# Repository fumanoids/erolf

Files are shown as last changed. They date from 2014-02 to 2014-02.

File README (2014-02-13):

              README FOR THE EROLF HARD- AND SOFTWARE RELEASE
            ===================================================

             2014-02-13 FUmanoids' Erolf Hardware Release v2014

          Copyright (c) 2014 FUmanoids / Freie Universität Berlin
                            All rights reserved

        For full license information, please refer to file LICENCE

Links:
       FUmanoids Homepage                           http://www.fumanoids.de
       FUmanoids on Facebook              http://www.facebook.com/fumanoids
       FUmanoids on Twitter                    http://twitter.com/fumanoids

       RoboCup Homepage                              http://www.robocup.org
       RoboCup Humanoid League Homepage          http://www.tzi.de/humanoid

This is part of the code/hardware release of team FUmanoids, version 2014. 

Our goal by releasing the source code and CAD files of components of our robot
is to provide some insight in humanoid soccer robot development, allowing other
teams to learn from our code and possibly our mistakes, but also to hopefully
encourage them to do the same and release their code as well. Though RoboCup is
a competition, it's also about research and finally to achieve our common goal -
to win against FIFA in 2050 ...

 1. PROJECT STRUCTURE
----------------------

The FUmanoids team has developed several software applications as well as our
own robots. The latter was developed internally and equipped with both
commercially available and self-built electronics.

This release addresses only the custom-built microcontroller board (named Erolf) 
used in the FUmanoid robots.

Neither a compiler, an SDK or CAD software is part of this package. In the
section "Getting Started" you find a list of recommended software to modify or
view the CAD files, to compile the software and to put the binaries onto the
processors.

 1.1 Overview of the package
-----------------------------

The project's root directory is "erolf" (the board's name).

The directories in the root directory are:

 - bin      -- some useful scripts and programs for building the program and
               documentation
 - build    -- All binary files of the program go here. This directory will
               be created during code compilation.
 - doc      -- The documentation directory. Here you can find some 
               documentation of the board. There are png files containing
               the schematics and the layout.
 - src      -- The actual source code.
               Note: The essential parts of the software is pretty well
               documented. Please consider this as a documentation 
               directory as well.
 - hardware -- Here you can find the CAD files for the PCB.

 2. THE EROLF PROJECT
------------------------- 

 2.1 Getting Started
-------------------------

 2.1.1 Software

The software is written in C with two extensions in assembler
(system_mutex_lock() and system_mutex_unlock()).

A compiler for the target hardware is not part of this package but can be picked
based on the user's preferences. We recommend using the arm-none-eabi-toolchain
(including gcc, ld and gdb) which can be found here:

                  https://launchpad.net/gcc-arm-embedded

 2.1.2 Hardware

To view the schematics and layout of this project we recommend using "CadSoft
EAGLE" which can be found at: http://www.cadsoftusa.com/

 2.1.3 Manufacturing

The PCB can be manufactured by most commonly known PCB services. A partlist can
be found in the folder where the schematics reside. But please double check the 
partlist since we cannot guarantee its completeness.

We chose every component on the board to be manually solderable. All you need is
a steady hand.

 2.1.4 Other Prerequisites
 
To flash the target a JTAG/SWD interface is needed.

We recommend using a "JLink" from Segger which supports JTAG and SWD for
flashing and debugging. Segger releases software acting as gdb-server and other
tools for common operating systems  (Linux, Mac, Windows). 

 2.2 Compiling the Software
---------------------------

The build system is based on premake 4. We include a more recent binary version
of premake4 than currently available in e.g. Ubuntu.. If you want the sourcecode
of premake have a look at http://industriousone.com/premake. Premake is licenced
under the terms of the BSD License.

The common IDE used for development in team FUmanoids is Eclipse/CDT which
is available at http://www.eclipse.org. Therefore we have the corresponding
project files added to our repository, to give an easy start. You can build the
code either by using Eclipse or by shell tools. Both ways are easy.
Other IDEs or editors can of course be used.

The build process generates two .elf files. One for each processor.

 2.2.1 Using Eclipse

If you choose to use Eclipse click File->Import and in the opening window
General->"Existing Project into Workspace" and choose the project's root
directory. Then you can compile the debug or release version of the software.

 2.2.2 Using the shell tools

You can simply run

 ./bin/compile.sh arm [release/debug]

to compile the code. This runs premake to generate the make-files and
runs "make" with the appropriate targets afterwards.

 2.3 Flashing the target
------------------------

In order to flash and debug the target software a JTAG/SWD Interface is needed.
Connect your debug interface to the processor you want to debug. For the pinning
information please consider looking in the schematics and the pinout information
of your JTAG/SWD interface.

In case you use a "JLink" from Segger start the JLinkGDBServer with the
parameter "-if swd" to use the Serial Wire Debug interface (similar to JTAG but
uses less wires). The output should tell you that a Cortex-M4 was identified.
If your debug interface cannot connect to the target doublecheck the power
supply and the pinning between your debug interface and the connector on
the PCB.

After your GDB-server is running you can use the flash.sh script (in the bin/
directory) to  flash the target. Use "./bin/flash.sh erolfP[1/2].elf".

In case you want to debug the software you can use the command line:

   run "arm-none-eabi-gdb"

In the following prompt enter:

   target remote localhost:2331
   monitor reset 0
   file erolfP[1/2].elf
   load
   monitor reset 0
   continue

In case you use Eclipse you can set up the "GDB Hardware Debugging" plugin for
this as well.

 4. REFERENCES
--------------

The framework used in this software was developed as part of the FUmanoid
project and is used in its power supply board as well (the project can be found
at http://www.fumanoids.de). The Berlin United Racing Team incorporates a
microcontroller board similar to the erolf which is operated by the framework as
well.

Many aspects of our work is described in the corresponding theses of our
students, which are available online at http://www.fumanoids.de/publications,
though most of them are in German.

This software uses libopencm3 which can be found at libopencm3.org.
Thank you very much for this project!

 5. CONTACT
-----------

We'd love to receive feedback, please feel free to contact us by email
at info@fumanoids.de. For information about our team and ongoing progress,
follow us on https://www.facebook.com/fumanoids, https://twitter.com/fumanoids
and http://www.fumanoids.de.

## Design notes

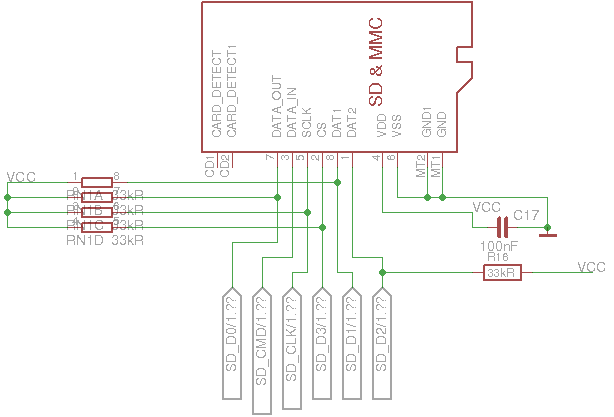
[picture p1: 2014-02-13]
doc/SCHEMATICS_sd_card.png

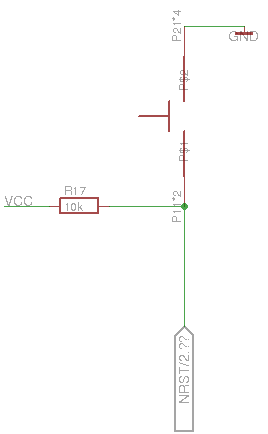
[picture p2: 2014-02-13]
doc/SCHEMATICS_reset_button.png

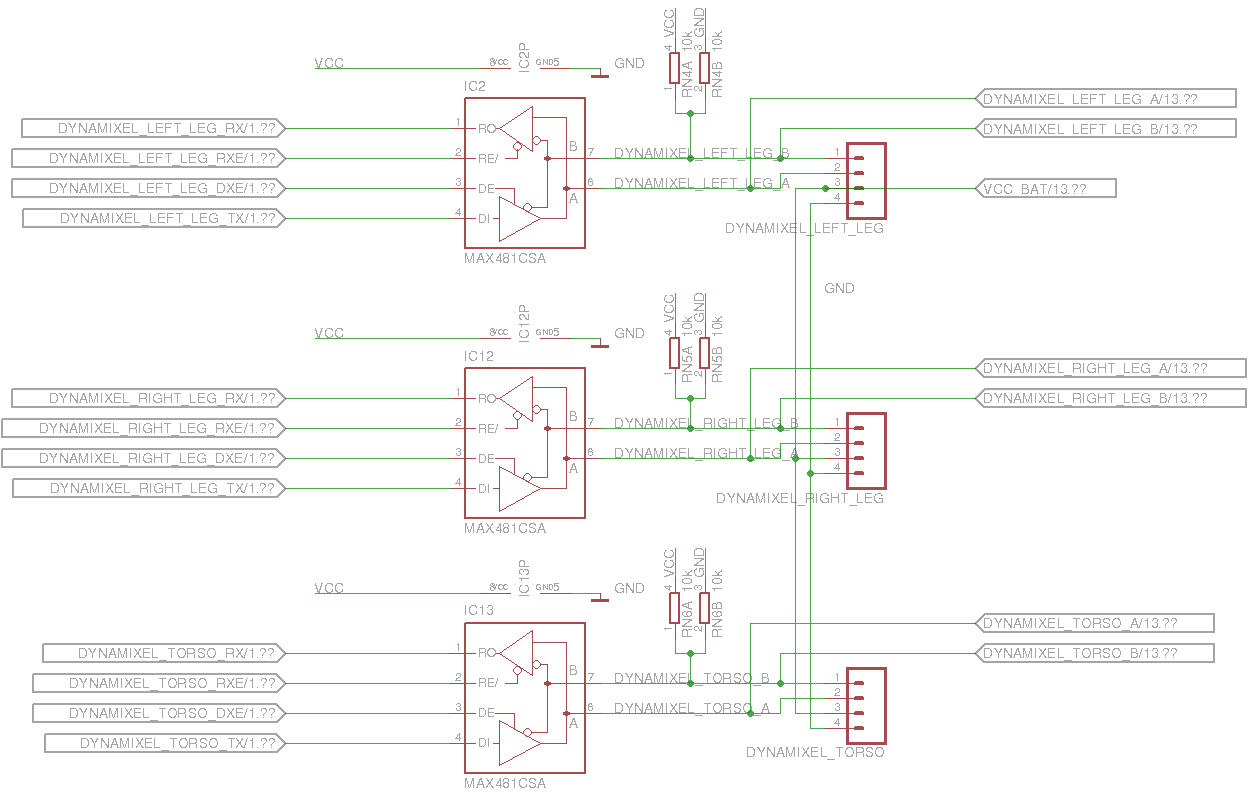
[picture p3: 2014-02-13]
doc/SCHEMATICS_rs485_interfaces.png

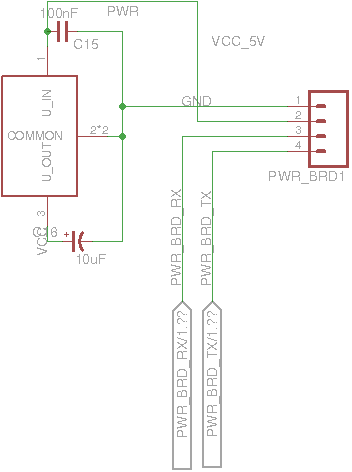
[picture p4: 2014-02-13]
doc/SCHEMATICS_voltage_regulator.png

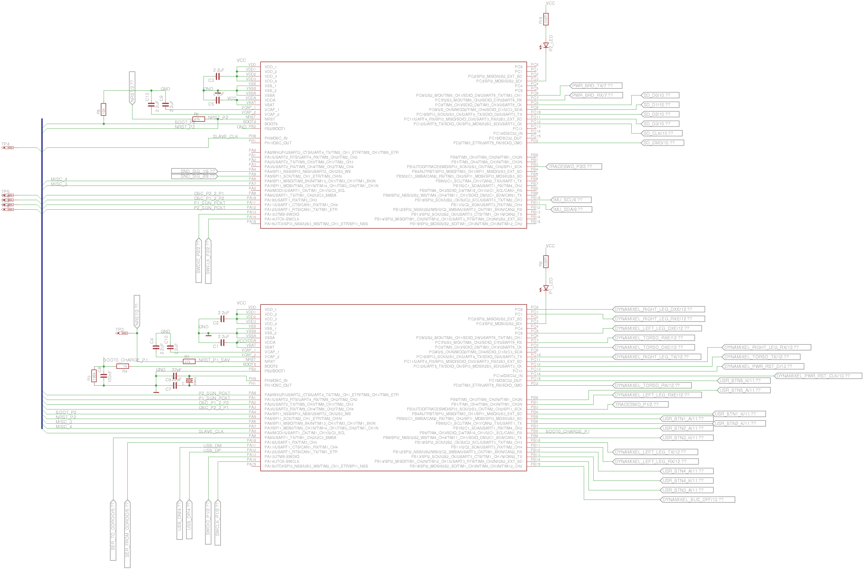
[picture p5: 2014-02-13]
doc/SCHEMATICS_processors.png

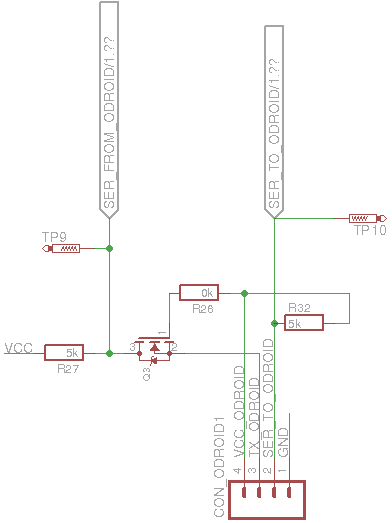
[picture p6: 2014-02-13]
doc/SCHEMATICS_communication_2_main_computer.png

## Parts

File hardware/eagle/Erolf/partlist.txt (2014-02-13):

Partlist

Exported from Erolf2.brd at 15 Aug 2013 12:00:02

EAGLE Version 6.5.0 Copyright (c) 1988-2013 CadSoft

Assembly variant: 

Part                Value              Package         Library                 Position (mm)         Orientation

############################# Kondensatoren

9x
C4                  2.2uF              C0603           rc-master               (10 14)               R90

2x
C6                  22pF               C0603           rc-master               (35 10)               MR180

3x
C8                  100nF              C0603           rc-master               (29 6)                MR0

############################# Stecker

6x
CON_ODROID1                            04P             con-amp-quick           (3 11)                R90

1x
X3                  MINI-USB-32005-301 32005-301       con-cypressindustries   (5.33 23.48)          R0

2x
X1                  53398-06           53398-06        con-molex               (21.96 3.09)          R180

1x
X5                  53398-10           53398-10        con-molex               (42 5)                R0

############################# Diskretes

1x
BLUBB                                  SOT223-4        texas                   (10.82 33.53)         MR270

6x
IC1                 TL331              DBV-R-PDSO-G5   linear                  (47 32)               MR270

3x
IC2                 MAX481CSA          SO08            maxim                   (47 22)               R270

1x
IC11                USB6B1             SO08            st-microelectronics     (10 23)               MR90

2x
P2_LED                                 CHIP-LED0805    adafruit                (29 29)               R0

2x
PROCESSOR_2         STM32-F405RB       LQFP-64         stm32                   (22 35)               R0

3x
Q1                  BSS123             SOT23           transistor-small-signal (40 38)               R0

# D-FF
1x
U$7                                    DCV_R-PDSO-6    texas                   (41.01 32.41)         MR90

# p-MOSFET
1x
U$6                 SI4459ADY          SO-8            vishay                  (46.01 38.23)         MR0

############################# Widerstaende

1x
R3                  100k               R0603           divers                  (25 4)                MR180

7x
R33                 330                R0603           divers                  (38 7)                MR90

6x
R2                  1k                 R0603           divers                  (40 33)               R180

10x
R13                 10k                R0603           divers                  (43 42)               R0

1x
R16                 33kR               R0603           divers                  (38 43)               MR180

1x
RN1                 33kR               EXBS8V          resistor-dil            (35 47)               MR180

4x
RN2                 10k                EXBV4V          resistor-dil            (47 42)               R90

############################# Misc

1x
U$2                 MICROSD            MICROSD         adafruit                (16 32)               MR180

1x
U$3                                    BUTTON          berlinunited            (10 35)               R270

1x
U$4                 MINI-IMU-9V2       PCB             miniIMU-9v2             (32 30)               R0

1x
Y1                  8MHz              CRYSTAL_4.9X1.8 microbuilder            (36 13)               R180

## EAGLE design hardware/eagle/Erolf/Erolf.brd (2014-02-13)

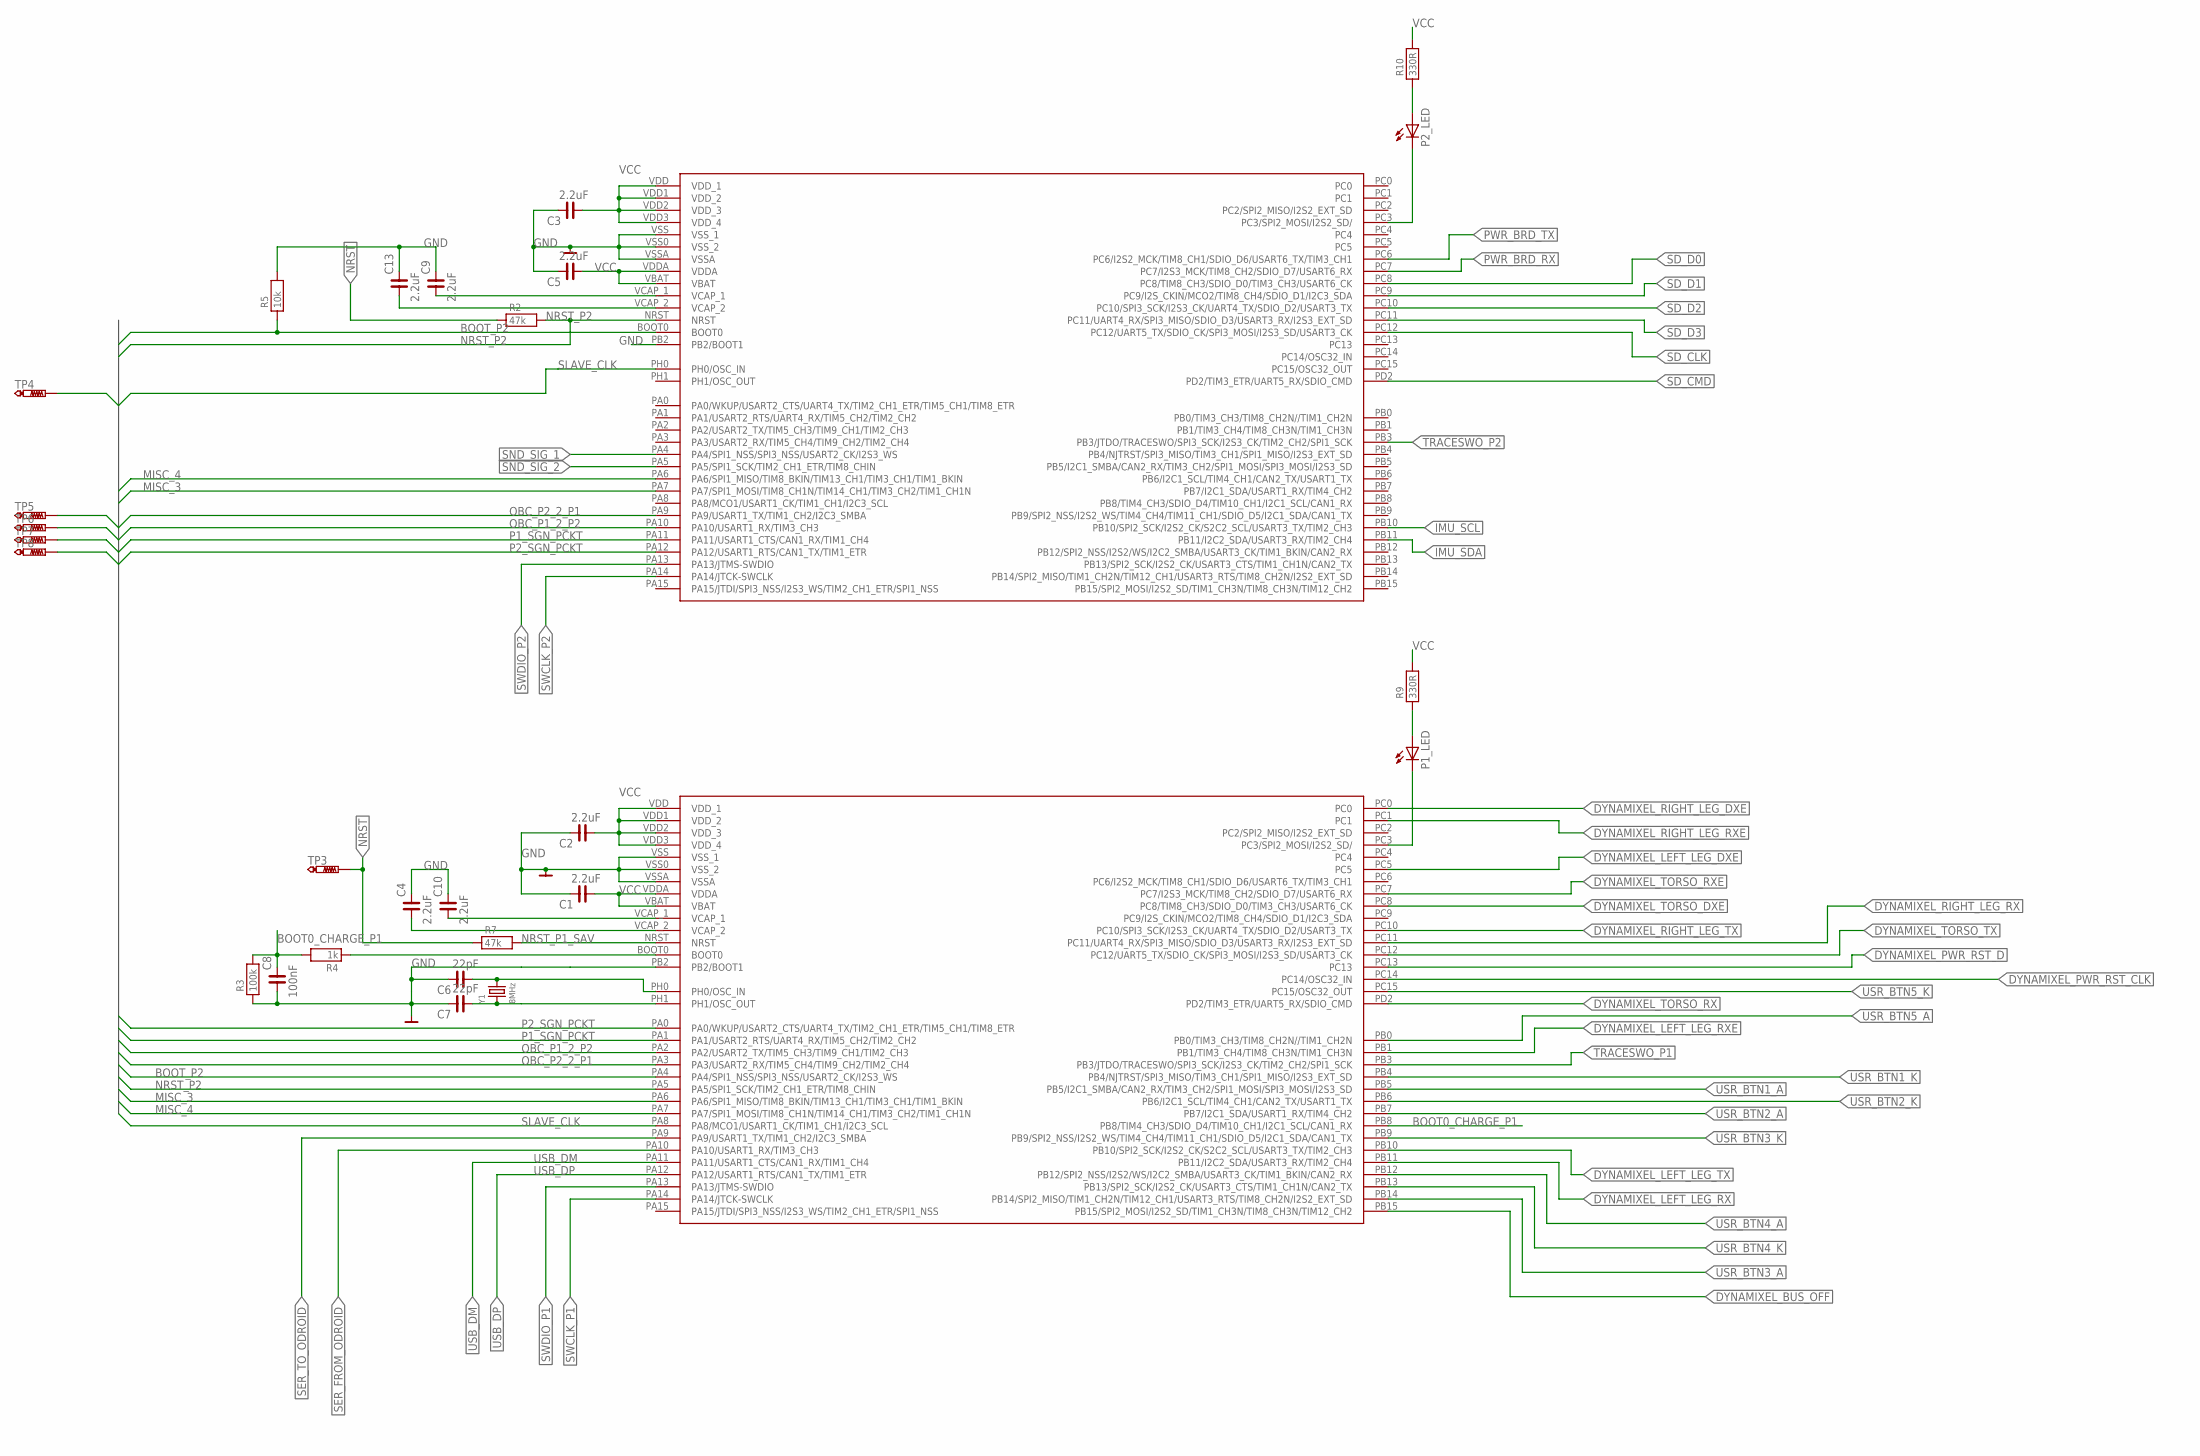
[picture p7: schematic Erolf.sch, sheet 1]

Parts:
C1, C2, C3, C4, C5, C9, C10, C13: 2.2uF; C0603
C6, C7: 22pF; C0603
C8: 100nF; C0603
P1_LED, P2_LED: LEDCHIP-LED0805; CHIP-LED0805
PROCESSOR_1, PROCESSOR_2: STM32-F405RB; LQFP-64
R2, R7: 47k; R0603
R3: 100k; R0603
R4: 1k; R0603
R5: 10k; R0603
R9, R10: 330R; R0603
TP3, TP4, TP5, TP6, TP7, TP8: PTR1TP06R; TP06R
Y1: 8MHz; CRYSTAL_4.9X1.8

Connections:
BOOT0_CHARGE_P1: C8.2, PROCESSOR_1.PB8 (PB8/TIM4_CH3/SDIO_D4/TIM10_CH1/I2C1_SCL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), R3.2, R4.2
BOOT_P2: PROCESSOR_1.PA4 (PA4/SPI1_NSS/SPI3_NSS/USART2_CK/I2S3_WS), PROCESSOR_2.BOOT0, R5.1
DYNAMIXEL_BUS_OFF: PROCESSOR_1.PB15 (PB15/SPI2_MOSI/I2S2_SD/TIM1_CH3N/TIM8_C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); also elsewhere on the board
DYNAMIXEL_LEFT_LEG_DXE: PROCESSOR_1.PC5; also elsewhere on the board
DYNAMIXEL_LEFT_LEG_RX: PROCESSOR_1.PB11 (PB11/I2C2_SDA/USART3_RX/TIM2_CH4); also elsewhere on the board
DYNAMIXEL_LEFT_LEG_RXE: PROCESSOR_1.PB1 (PB1/TIM3_CH4/TIM8_CH3N/TIM1_CH3N); also elsewhere on the board
DYNAMIXEL_LEFT_LEG_TX: PROCESSOR_1.PB10 (PB10/SPI2_SCK/I2S2_CK/S2C2_SCL/USART3_T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); also elsewhere on the board
DYNAMIXEL_PWR_RST_CLK: PROCESSOR_1.PC14 (PC14/OSC32_IN); also elsewhere on the board
DYNAMIXEL_PWR_RST_D: PROCESSOR_1.PC13; also elsewhere on the board
DYNAMIXEL_RIGHT_LEG_DXE: PROCESSOR_1.PC0; also elsewhere on the board
DYNAMIXEL_RIGHT_LEG_RX: PROCESSOR_1.PC11 (PC11/UART4_RX/SPI3_MISO/SDIO_D3/USART3_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); also elsewhere on the board
DYNAMIXEL_RIGHT_LEG_RXE: PROCESSOR_1.PC1; also elsewhere on the board
DYNAMIXEL_RIGHT_LEG_TX: PROCESSOR_1.PC10 (PC10/SPI3_SCK/I2S3_CK/UART4_TX/SDIO_D2/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); also elsewhere on the board
DYNAMIXEL_TORSO_DXE: PROCESSOR_1.PC8 (PC8/TIM8_CH3/SDIO_D0/TIM3_CH3/USART6_CK); also elsewhere on the board
DYNAMIXEL_TORSO_RX: PROCESSOR_1.PD2 (PD2/TIM3_ETR/UART5_RX/SDIO_CMD); also elsewhere on the board
DYNAMIXEL_TORSO_RXE: PROCESSOR_1.PC7 (PC7/I2S3_MCK/TIM8_CH2/SDIO_D7/USART6_RX); also elsewhere on the board
DYNAMIXEL_TORSO_TX: PROCESSOR_1.PC12 (PC12/UART5_TX/SDIO_CK/SPI3_MOSI/I2S3_SD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); also elsewhere on the board
GND: C1.2, C2.2, C3.2, C4.2, C5.2, C6.2, C7.2, C8.1, C9.2, C10.2, C13.2, PROCESSOR_1.PB2 (PB2/BOOT1), PROCESSOR_1.VSS (VSS_1), PROCESSOR_1.VSS0 (VSS_2), PROCESSOR_1.VSSA, PROCESSOR_2.PB2 (PB2/BOOT1), PROCESSOR_2.VSS (VSS_1), PROCESSOR_2.VSS0 (VSS_2), PROCESSOR_2.VSSA, R3.1, R5.2; also elsewhere on the board
IMU_SCL: PROCESSOR_2.PB10 (PB10/SPI2_SCK/I2S2_CK/S2C2_SCL/USART3_T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); also elsewhere on the board
IMU_SDA: PROCESSOR_2.PB11 (PB11/I2C2_SDA/USART3_RX/TIM2_CH4); also elsewhere on the board
MISC_3: PROCESSOR_1.PA6 (PA6/SPI1_MISO/TIM8_BKIN/TIM13_CH1/TIM3_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), PROCESSOR_2.PA7 (PA7/SPI1_MOSI/TIM8_CH1N/TIM14_CH1/TIM3_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)
MISC_4: PROCESSOR_1.PA7 (PA7/SPI1_MOSI/TIM8_CH1N/TIM14_CH1/TIM3_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), PROCESSOR_2.PA6 (PA6/SPI1_MISO/TIM8_BKIN/TIM13_CH1/TIM3_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)
unnamed: C10.1, PROCESSOR_1.VCAP_1
unnamed: P1_LED.A, R9.1
unnamed: P2_LED.A, R10.1
unnamed: P1_LED.C, PROCESSOR_1.PC3 (PC3/SPI2_MOSI/I2S2_SD/)
unnamed: C13.1, PROCESSOR_2.VCAP_2
unnamed: C9.1, PROCESSOR_2.VCAP_1
unnamed: PROCESSOR_1.BOOT0, R4.1
unnamed: P2_LED.C, PROCESSOR_2.PC3 (PC3/SPI2_MOSI/I2S2_SD/)
unnamed: C4.1, PROCESSOR_1.VCAP_2
NRST: R2.1, R7.1, TP3.TP; also elsewhere on the board
NRST_P1_SAV: PROCESSOR_1.NRST, R7.2
NRST_P2: PROCESSOR_1.PA5 (PA5/SPI1_SCK/TIM2_CH1_ETR/TIM8_CHIN), PROCESSOR_2.NRST, R2.2
OBC_P1_2_P2: PROCESSOR_1.PA2 (PA2/USART2_TX/TIM5_CH3/TIM9_CH1/TIM2_CH3), PROCESSOR_2.PA10 (PA10/USART1_RX/TIM3_CH3), TP6.TP
OBC_P2_2_P1: PROCESSOR_1.PA3 (PA3/USART2_RX/TIM5_CH4/TIM9_CH2/TIM2_CH4), PROCESSOR_2.PA9 (PA9/USART1_TX/TIM1_CH2/I2C3_SMBA), TP5.TP
OSC_IN: C6.1, PROCESSOR_1.PH0 (PH0/OSC_IN), Y1.2
OSC_OUT: C7.1, PROCESSOR_1.PH1 (PH1/OSC_OUT), Y1.1
P1_SGN_PCKT: PROCESSOR_1.PA1 (PA1/USART2_RTS/UART4_RX/TIM5_CH2/TIM2_C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), PROCESSOR_2.PA11 (PA11/USART1_CTS/CAN1_RX/TIM1_CH4), TP7.TP
P2_SGN_PCKT: PROCESSOR_1.PA0 (PA0/WKUP/USART2_CTS/UART4_TX/TIM2_CH1_E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), PROCESSOR_2.PA12 (PA12/USART1_RTS/CAN1_TX/TIM1_ETR), TP8.TP
PWR_BRD_RX: PROCESSOR_2.PC7 (PC7/I2S3_MCK/TIM8_CH2/SDIO_D7/USART6_RX); also elsewhere on the board
PWR_BRD_TX: PROCESSOR_2.PC6 (PC6/I2S2_MCK/TIM8_CH1/SDIO_D6/USART6_TX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); also elsewhere on the board
SD_CLK: PROCESSOR_2.PC12 (PC12/UART5_TX/SDIO_CK/SPI3_MOSI/I2S3_SD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); also elsewhere on the board
SD_CMD: PROCESSOR_2.PD2 (PD2/TIM3_ETR/UART5_RX/SDIO_CMD); also elsewhere on the board
SD_D0: PROCESSOR_2.PC8 (PC8/TIM8_CH3/SDIO_D0/TIM3_CH3/USART6_CK); also elsewhere on the board
SD_D1: PROCESSOR_2.PC9 (PC9/I2S_CKIN/MCO2/TIM8_CH4/SDIO_D1/I2C3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); also elsewhere on the board
SD_D2: PROCESSOR_2.PC10 (PC10/SPI3_SCK/I2S3_CK/UART4_TX/SDIO_D2/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); also elsewhere on the board
SD_D3: PROCESSOR_2.PC11 (PC11/UART4_RX/SPI3_MISO/SDIO_D3/USART3_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); also elsewhere on the board
SER_FROM_ODROID: PROCESSOR_1.PA10 (PA10/USART1_RX/TIM3_CH3); also elsewhere on the board
SER_TO_ODROID: PROCESSOR_1.PA9 (PA9/USART1_TX/TIM1_CH2/I2C3_SMBA); also elsewhere on the board
SLAVE_CLK: PROCESSOR_1.PA8 (PA8/MCO1/USART1_CK/TIM1_CH1/I2C3_SCL), PROCESSOR_2.PH0 (PH0/OSC_IN), TP4.TP
SND_SIG_1: PROCESSOR_2.PA4 (PA4/SPI1_NSS/SPI3_NSS/USART2_CK/I2S3_WS); also elsewhere on the board
SND_SIG_2: PROCESSOR_2.PA5 (PA5/SPI1_SCK/TIM2_CH1_ETR/TIM8_CHIN); also elsewhere on the board
SWCLK_P1: PROCESSOR_1.PA14 (PA14/JTCK-SWCLK); also elsewhere on the board
SWCLK_P2: PROCESSOR_2.PA14 (PA14/JTCK-SWCLK); also elsewhere on the board
SWDIO_P1: PROCESSOR_1.PA13 (PA13/JTMS-SWDIO); also elsewhere on the board
SWDIO_P2: PROCESSOR_2.PA13 (PA13/JTMS-SWDIO); also elsewhere on the board
TRACESWO_P1: PROCESSOR_1.PB3 (PB3/JTDO/TRACESWO/SPI3_SCK/I2S3_CK/TIM2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); also elsewhere on the board
TRACESWO_P2: PROCESSOR_2.PB3 (PB3/JTDO/TRACESWO/SPI3_SCK/I2S3_CK/TIM2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); also elsewhere on the board
USB_DM: PROCESSOR_1.PA11 (PA11/USART1_CTS/CAN1_RX/TIM1_CH4); also elsewhere on the board
USB_DP: PROCESSOR_1.PA12 (PA12/USART1_RTS/CAN1_TX/TIM1_ETR); also elsewhere on the board
USR_BTN1_A: PROCESSOR_1.PB5 (PB5/I2C1_SMBA/CAN2_RX/TIM3_CH2/SPI1_MOS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); also elsewhere on the board
USR_BTN1_K: PROCESSOR_1.PB4 (PB4/NJTRST/SPI3_MISO/TIM3_CH1/SPI1_MISO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); also elsewhere on the board
USR_BTN2_A: PROCESSOR_1.PB7 (PB7/I2C1_SDA/USART1_RX/TIM4_CH2); also elsewhere on the board
USR_BTN2_K: PROCESSOR_1.PB6 (PB6/I2C1_SCL/TIM4_CH1/CAN2_TX/USART1_TX); also elsewhere on the board
USR_BTN3_A: PROCESSOR_1.PB14 (PB14/SPI2_MISO/TIM1_CH2N/TIM12_CH1/USAR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); also elsewhere on the board
USR_BTN3_K: PROCESSOR_1.PB9 (PB9/SPI2_NSS/I2S2_WS/TIM4_CH4/TIM11_CH1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); also elsewhere on the board
USR_BTN4_A: PROCESSOR_1.PB12 (PB12/SPI2_NSS/I2S2/WS/I2C2_SMBA/USART3_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); also elsewhere on the board
USR_BTN4_K: PROCESSOR_1.PB13 (PB13/SPI2_SCK/I2S2_CK/USART3_CTS/TIM1_C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); also elsewhere on the board
USR_BTN5_A: PROCESSOR_1.PB0 (PB0/TIM3_CH3/TIM8_CH2N//TIM1_CH2N); also elsewhere on the board
USR_BTN5_K: PROCESSOR_1.PC15 (PC15/OSC32_OUT); also elsewhere on the board
VCC: C1.1, C2.1, C3.1, C5.1, PROCESSOR_1.VBAT, PROCESSOR_1.VDD (VDD_1), PROCESSOR_1.VDD1 (VDD_2), PROCESSOR_1.VDD2 (VDD_3), PROCESSOR_1.VDD3 (VDD_4), PROCESSOR_1.VDDA, PROCESSOR_2.VBAT, PROCESSOR_2.VDD (VDD_1), PROCESSOR_2.VDD1 (VDD_2), PROCESSOR_2.VDD2 (VDD_3), PROCESSOR_2.VDD3 (VDD_4), PROCESSOR_2.VDDA, R9.2, R10.2; also elsewhere on the board

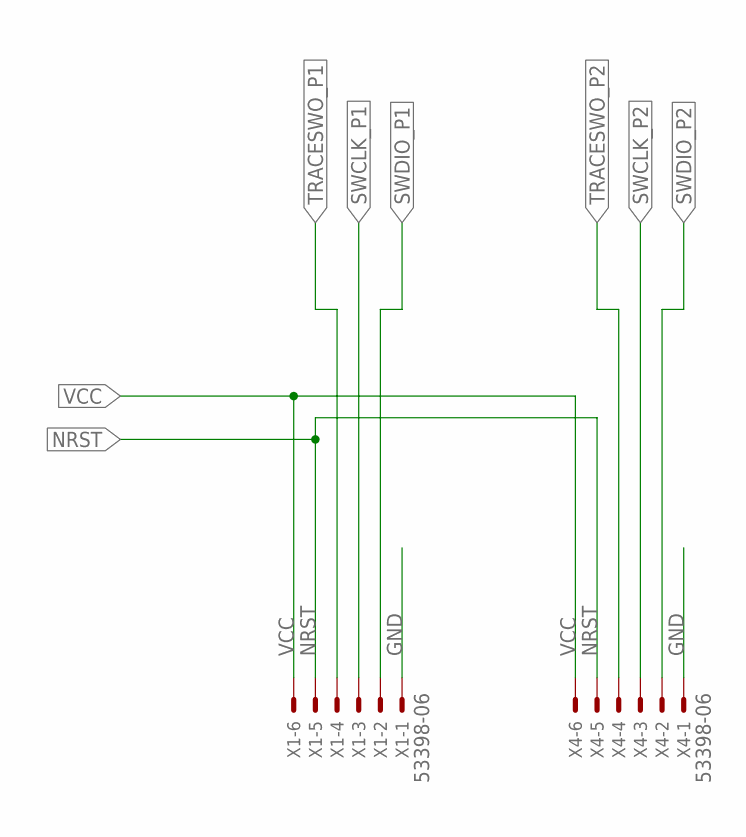
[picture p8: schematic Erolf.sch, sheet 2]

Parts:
X1, X4: 53398-06

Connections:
GND: X1.1, X4.1; also elsewhere on the board
NRST: X1.5, X4.5; also elsewhere on the board
SWCLK_P1: X1.3; also elsewhere on the board
SWCLK_P2: X4.3; also elsewhere on the board
SWDIO_P1: X1.2; also elsewhere on the board
SWDIO_P2: X4.2; also elsewhere on the board
TRACESWO_P1: X1.4; also elsewhere on the board
TRACESWO_P2: X4.4; also elsewhere on the board
VCC: X1.6, X4.6; also elsewhere on the board

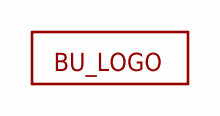
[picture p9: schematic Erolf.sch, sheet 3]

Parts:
U$8: LOGO

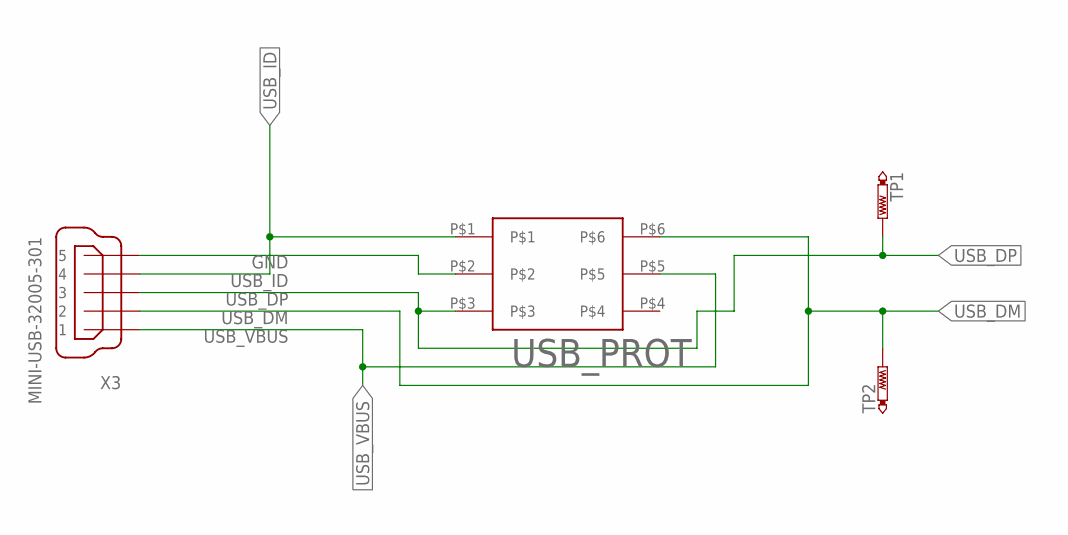
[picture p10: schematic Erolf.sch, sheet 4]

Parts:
TP1, TP2: PTR1TP06R; TP06R
USB_PROT: VBUS054B; LLP75-6L; DIGIKEY 751-1453-1-ND
X3: MINI-USB-32005-301; 32005-301

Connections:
GND: USB_PROT.P$2, X3.5; also elsewhere on the board
USB_DM: TP2.TP, USB_PROT.P$6, X3.2; also elsewhere on the board
USB_DP: TP1.TP, USB_PROT.P$3, X3.3; also elsewhere on the board
USB_ID: USB_PROT.P$1, X3.4
USB_VBUS: USB_PROT.P$5, X3.1

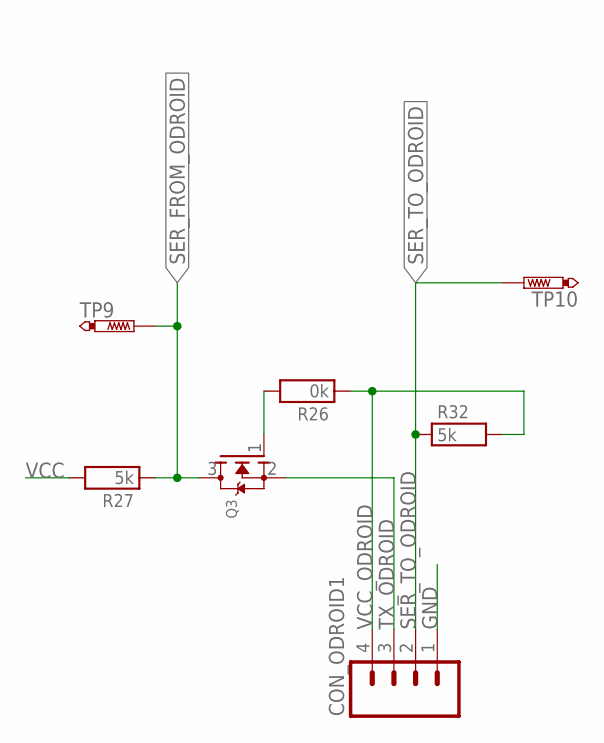
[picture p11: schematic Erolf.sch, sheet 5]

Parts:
CON_ODROID1: M04; 04P
Q3: MOSFET-NREFLOW; SOT23
R26: 0k; R0603
R27, R32: 5k; R0603
TP9, TP10: PTR1TP06R; TP06R

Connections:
GND: CON_ODROID1.1; also elsewhere on the board
unnamed: Q3.1 (G), R26.2
SER_FROM_ODROID: Q3.3 (D), R27.1, TP9.TP; also elsewhere on the board
SER_TO_ODROID: CON_ODROID1.2, R32.1, TP10.TP; also elsewhere on the board
TX_ODROID: CON_ODROID1.3, Q3.2 (S)
VCC: R27.2; also elsewhere on the board
VCC_ODROID: CON_ODROID1.4, R26.1, R32.2

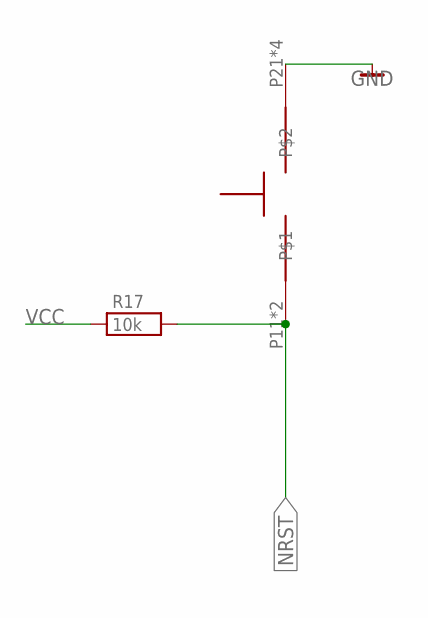
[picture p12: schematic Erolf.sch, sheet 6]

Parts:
R17: 10k; R0603
U$3: BUTTON

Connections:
GND: U$3.P21, U$3.P22, U$3.P23, U$3.P24; also elsewhere on the board
NRST: R17.2, U$3.P11, U$3.P12; also elsewhere on the board
VCC: R17.1; also elsewhere on the board

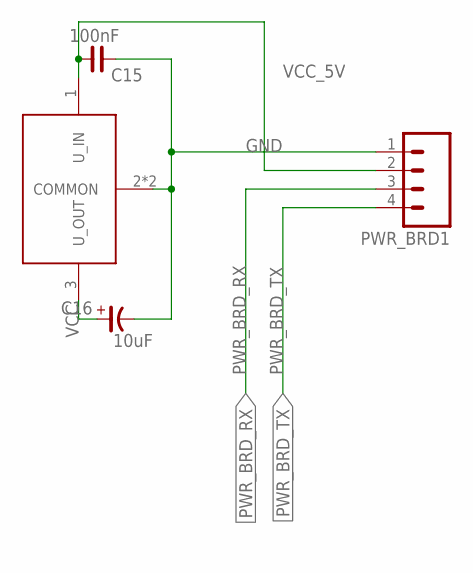
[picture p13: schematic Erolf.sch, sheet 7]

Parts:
BLUBB: UA78M00; SOT223-4
C15: 100nF; C0603
C16: 10uF; CE-025X060
PWR_BRD1: M04; 04P

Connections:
GND: BLUBB.2 (COMMON), BLUBB.4 (COMMON), C15.2, C16.-, PWR_BRD1.1; also elsewhere on the board
PWR_BRD_RX: PWR_BRD1.3; also elsewhere on the board
PWR_BRD_TX: PWR_BRD1.4; also elsewhere on the board
VCC: BLUBB.3 (U_OUT), C16.+; also elsewhere on the board
VCC_5V: BLUBB.1 (U_IN), C15.1, PWR_BRD1.2; also elsewhere on the board

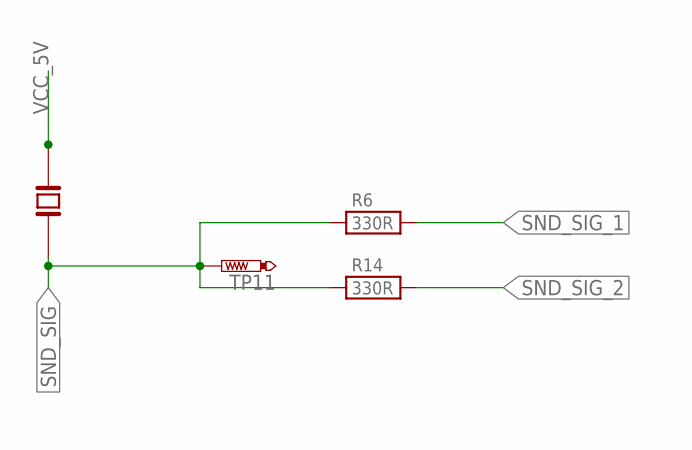
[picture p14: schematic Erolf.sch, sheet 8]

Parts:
R6, R14: 330R; R0603
TP11: PTR1TP06R; TP06R
U$1: PS1240P02CT3

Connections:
SND_SIG: R6.1, R14.1, TP11.TP, U$1.P$2
SND_SIG_1: R6.2; also elsewhere on the board
SND_SIG_2: R14.2; also elsewhere on the board
VCC_5V: U$1.P$1; also elsewhere on the board

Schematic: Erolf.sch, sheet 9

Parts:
U$4: MINI-IMU-9V2; PCB

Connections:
GND: U$4.GND; also elsewhere on the board
IMU_SCL: U$4.SCL; also elsewhere on the board
IMU_SDA: U$4.SDA; also elsewhere on the board
VCC: U$4.VDD, U$4.VIN; also elsewhere on the board

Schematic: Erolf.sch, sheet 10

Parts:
C17: 100nF; C0603
R16: 33kR; R0603
RN1: 33kR; EXBS8V
U$2: MICROSD

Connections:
GND: C17.2, U$2.6 (VSS), U$2.MT1 (GND), U$2.MT2 (GND1); also elsewhere on the board
SD_CLK: RN1.6 (2), U$2.5 (SCLK); also elsewhere on the board
SD_CMD: U$2.3 (DATA_IN); also elsewhere on the board
SD_D0: RN1.7 (2), U$2.7 (DATA_OUT); also elsewhere on the board
SD_D1: RN1.8 (2), U$2.8 (DAT1); also elsewhere on the board
SD_D2: R16.1, U$2.1 (DAT2); also elsewhere on the board
SD_D3: RN1.5 (2), U$2.2 (CS); also elsewhere on the board
VCC: C17.1, R16.2, RN1.1, RN1.2 (1), RN1.3 (1), RN1.4 (1), U$2.4 (VDD); also elsewhere on the board

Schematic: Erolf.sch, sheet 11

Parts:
R1, R8, R11, R12, R33: 330R; R0603
R34, R35, R36, R37, R38: 10kR; R0603
X2: 53261-10

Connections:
USR_BTN1_A: R38.2, X2.9; also elsewhere on the board
USR_BTN1_K: R33.1, X2.10; also elsewhere on the board
USR_BTN2_A: R37.2, X2.7; also elsewhere on the board
USR_BTN2_K: R12.1, X2.8; also elsewhere on the board
USR_BTN3_A: R36.2, X2.5; also elsewhere on the board
USR_BTN3_K: R11.1, X2.6; also elsewhere on the board
USR_BTN4_A: R35.2, X2.3; also elsewhere on the board
USR_BTN4_K: R8.1, X2.4; also elsewhere on the board
USR_BTN5_A: R34.2, X2.1; also elsewhere on the board
USR_BTN5_K: R1.1, X2.2; also elsewhere on the board
VCC: R1.2, R8.2, R11.2, R12.2, R33.2, R34.1, R35.1, R36.1, R37.1, R38.1; also elsewhere on the board

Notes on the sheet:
when using buttons with embedded LED connect the LED's anode with one pin of the button and the LED's cathode with the other pin of the button. The LED's anode shall be connected to USR_BTNx_A and the cathode to USR_BTNx_K

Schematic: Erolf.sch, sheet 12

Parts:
DYNAMIXEL_LEFT_LEG: M04; 04P
DYNAMIXEL_RIGHT_LEG: M04; 04P
DYNAMIXEL_TORSO: M04; 04P
IC2, IC12, IC13: MAX481CSA; SO08
RN4, RN5, RN6: 10k; EXBV4V

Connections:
DYNAMIXEL_LEFT_LEG_A: DYNAMIXEL_LEFT_LEG.2, IC2.6 (A); also elsewhere on the board
DYNAMIXEL_LEFT_LEG_B: DYNAMIXEL_LEFT_LEG.1, IC2.7 (B), RN4.1, RN4.2 (1); also elsewhere on the board
DYNAMIXEL_LEFT_LEG_DXE: IC2.3 (DE); also elsewhere on the board
DYNAMIXEL_LEFT_LEG_RX: IC2.1 (RO); also elsewhere on the board
DYNAMIXEL_LEFT_LEG_RXE: IC2.2 (RE/); also elsewhere on the board
DYNAMIXEL_LEFT_LEG_TX: IC2.4 (DI); also elsewhere on the board
DYNAMIXEL_RIGHT_LEG_A: DYNAMIXEL_RIGHT_LEG.2, IC12.6 (A); also elsewhere on the board
DYNAMIXEL_RIGHT_LEG_B: DYNAMIXEL_RIGHT_LEG.1, IC12.7 (B), RN5.1, RN5.2 (1); also elsewhere on the board
DYNAMIXEL_RIGHT_LEG_DXE: IC12.3 (DE); also elsewhere on the board
DYNAMIXEL_RIGHT_LEG_RX: IC12.1 (RO); also elsewhere on the board
DYNAMIXEL_RIGHT_LEG_RXE: IC12.2 (RE/); also elsewhere on the board
DYNAMIXEL_RIGHT_LEG_TX: IC12.4 (DI); also elsewhere on the board
DYNAMIXEL_TORSO_A: DYNAMIXEL_TORSO.2, IC13.6 (A); also elsewhere on the board
DYNAMIXEL_TORSO_B: DYNAMIXEL_TORSO.1, IC13.7 (B), RN6.1, RN6.2 (1); also elsewhere on the board
DYNAMIXEL_TORSO_DXE: IC13.3 (DE); also elsewhere on the board
DYNAMIXEL_TORSO_RX: IC13.1 (RO); also elsewhere on the board
DYNAMIXEL_TORSO_RXE: IC13.2 (RE/); also elsewhere on the board
DYNAMIXEL_TORSO_TX: IC13.4 (DI); also elsewhere on the board
GND: DYNAMIXEL_LEFT_LEG.4, DYNAMIXEL_RIGHT_LEG.4, DYNAMIXEL_TORSO.4, IC2.5 (GND), IC12.5 (GND), IC13.5 (GND), RN4.3 (2), RN5.3 (2), RN6.3 (2); also elsewhere on the board
VCC: IC2.8 (VCC), IC12.8 (VCC), IC13.8 (VCC), RN4.4 (2), RN5.4 (2), RN6.4 (2); also elsewhere on the board
VCC_BAT: DYNAMIXEL_LEFT_LEG.3, DYNAMIXEL_RIGHT_LEG.3, DYNAMIXEL_TORSO.3; also elsewhere on the board

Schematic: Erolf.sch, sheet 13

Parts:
C11: 100nF; C0603
D1: ZENER-DIODESOD80C; SOD80C
D2: DIODE-MICROMELF-R; MICROMELF-R
DYNAMIXEL_PWR: M04; 04P
IC1, IC3, IC4, IC5, IC6, IC7: TL331; DBV-R-PDSO-G5
Q1: BSS123; SOT23
R13, R18, R23: 10kR; R0603
R15: 1kR; R0603
TP20, TP21, TP22: PTR1TP06R; TP06R
U$6: SI4459ADY; SO-8
U$7: SN74LVC1G175; DCV_R-PDSO-6

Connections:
DYNAMIXEL_BUS_OFF: Q1.1 (G), R15.2; also elsewhere on the board
DYNAMIXEL_BUS_OFF_AUTO_TRIG: IC1.4 (OUT), IC3.4 (OUT), IC4.4 (OUT), IC5.4 (OUT), IC6.4 (OUT), IC7.4 (OUT), R23.2, TP20.TP, U$7.P$6 (NCLR)
DYNAMIXEL_LEFT_LEG_A: IC5.1 (-IN); also elsewhere on the board
DYNAMIXEL_LEFT_LEG_B: IC6.1 (-IN); also elsewhere on the board
DYNAMIXEL_PWR_RST_CLK: U$7.P$1 (CLK); also elsewhere on the board
DYNAMIXEL_PWR_RST_D: U$7.P$3 (D); also elsewhere on the board
DYNAMIXEL_RIGHT_LEG_A: IC4.1 (-IN); also elsewhere on the board
DYNAMIXEL_RIGHT_LEG_B: IC3.1 (-IN); also elsewhere on the board
DYNAMIXEL_TORSO_A: DYNAMIXEL_PWR.2, IC7.1 (-IN); also elsewhere on the board
DYNAMIXEL_TORSO_B: DYNAMIXEL_PWR.1, IC1.1 (-IN); also elsewhere on the board
GND: C11.2, D1.A, DYNAMIXEL_PWR.4, IC1.2 (GND), IC3.2 (GND), IC4.2 (GND), IC5.2 (GND), IC6.2 (GND), IC7.2 (GND), Q1.2 (S), U$7.P$2 (GND); also elsewhere on the board
unnamed: R15.1, U$7.P$4 (Q)
unnamed: Q1.3 (D), R13.1, U$6.P4 (G)
unnamed: D2.C, R18.1
VCC: R23.1, U$7.P$5 (VCC); also elsewhere on the board
VCC_BAT: TP22.TP, U$6.P5 (D), U$6.P6 (D), U$6.P7 (D), U$6.P8 (D); also elsewhere on the board
VCC_BAT_PRE: D2.A, DYNAMIXEL_PWR.3, IC1.5 (V+), IC3.5 (V+), IC4.5 (V+), IC5.5 (V+), IC6.5 (V+), IC7.5 (V+), R13.2, U$6.P1 (S), U$6.P2 (S), U$6.P3 (S)
V_SAFETY_REF: C11.1, D1.C, IC1.3 (+IN), IC3.3 (+IN), IC4.3 (+IN), IC5.3 (+IN), IC6.3 (+IN), IC7.3 (+IN), R18.2, TP21.TP

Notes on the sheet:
the recommended value of this Z-Diode is about the maximum allowed voltage of the RS485 transceivers (usually 12V) minus some margin (2V suffice) 10 Volts is usually a good measure

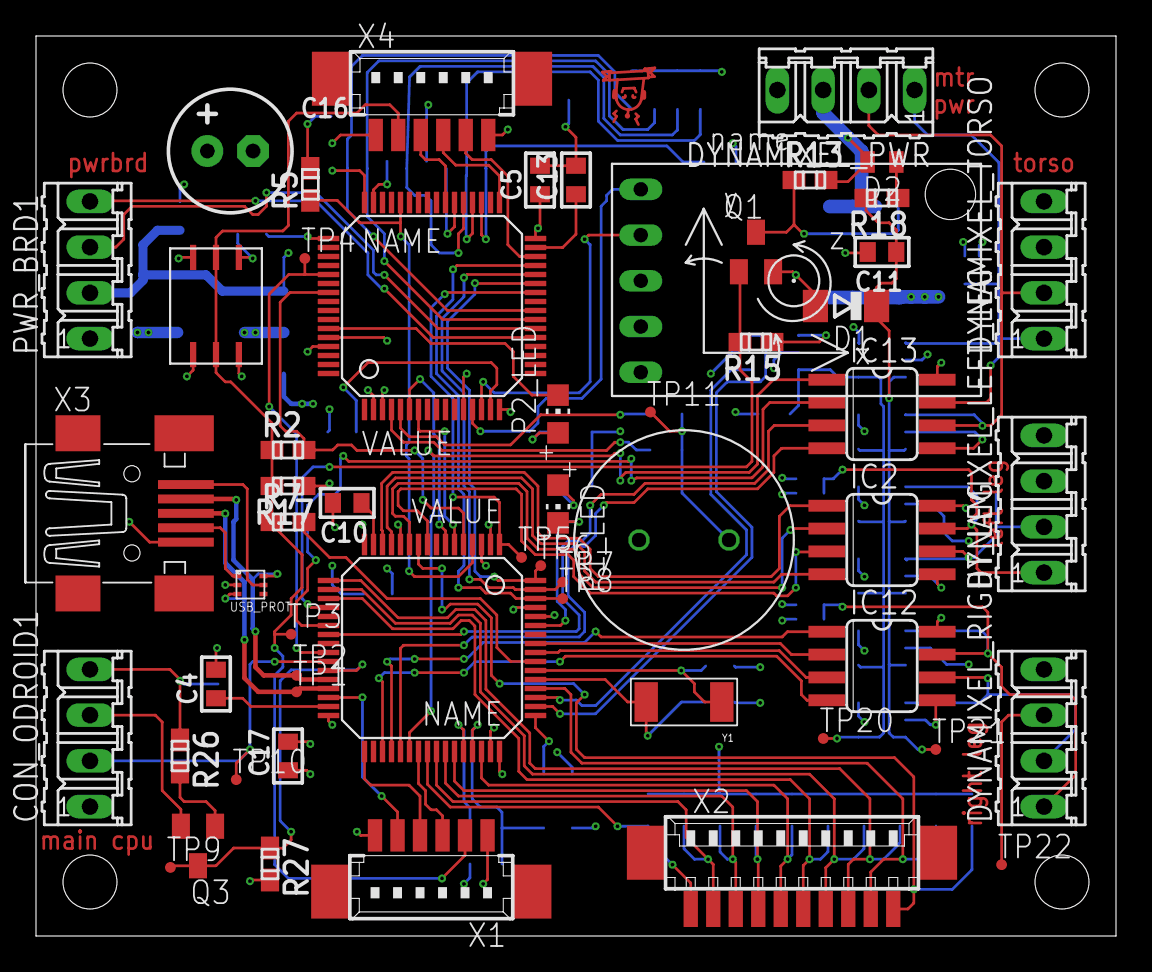
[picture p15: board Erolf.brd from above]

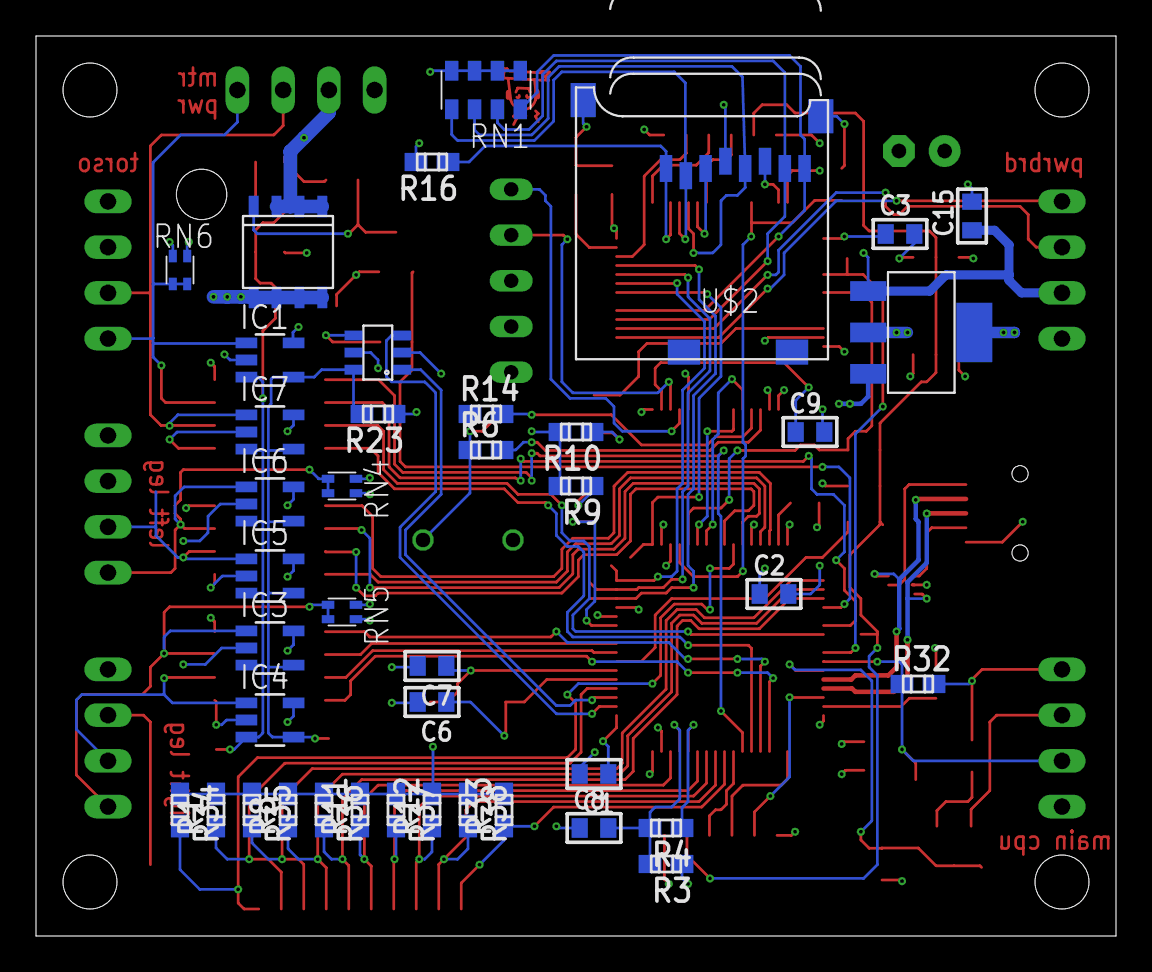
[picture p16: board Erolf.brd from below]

Board: 4 copper layers, 60.0 x 50.0 mm, 98 parts (41 on the bottom side), 92 nets.

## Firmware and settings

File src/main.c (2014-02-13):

/*
 * main.c
 *
 *  Created on: Oct 17, 2012
 *      Author: lutz
 */

#include <flawless/init/systemInitializer.h>

#include <flawless/core/msg_msgPump.h>

#include <flawless/logging/logging.h>

int main(void)
{
	systemInitialize();

	LOG_VERBOSE_0("all intialized");

	msgPump_pumpMessage();

	return 0;
}

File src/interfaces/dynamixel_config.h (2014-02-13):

/*
 * dynamixel_config.h
 *
 *  Created on: Dec 1, 2012
 *      Author: lutz
 */

#ifndef DYNAMIXEL_CONFIG_H_
#define DYNAMIXEL_CONFIG_H_


typedef enum tag_instruction
{
	DYNAMIXEL_INSTRUCTION_PING        = 0x1,
	DYNAMIXEL_INSTRUCTION_READ        = 0x2,
	DYNAMIXEL_INSTRUCTION_WRITE       = 0x3,
	DYNAMIXEL_INSTRUCTION_REG_WRITE   = 0x4,
	DYNAMIXEL_INSTRUCTION_ACTION      = 0x5,
	DYNAMIXEL_INSTRUCTION_RESET       = 0x6,
	DYNAMIXEL_INSTRUCTION_SYNC_WRITE  = 0x83
} dynamixelInstruction_t;


enum tag_dynamixel_register
{
	DYNAMIXEL_REGISTER_ID = 0x3,
	DYNAMIXEL_REGISTER_BAUD_RATE = 0x4,
	DYNAMIXEL_REGISTER_RETURN_DELAY_TIME = 0x5,
	DYNAMIXEL_REGISTER_CW_ANGLE_LIMIT = 0x6,
	DYNAMIXEL_REGISTER_CCW_ANGLE_LIMIT = 0x8,
	DYNAMIXEL_REGISTER_TEMP_H_LIMIT = 0xb,
	DYNAMIXEL_REGISTER_VOLT_L_LIMIT = 0xc,
	DYNAMIXEL_REGISTER_VOLT_H_LIMIT = 0xd,
	DYNAMIXEL_REGISTER_MAX_TORQUE = 0xe,
	DYNAMIXEL_REGISTER_STATUS_RETURN_LEVEL = 0x10,
	DYNAMIXEL_REGISTER_ALARM_LED = 0x11,
	DYNAMIXEL_REGISTER_ALARM_SHUTDOWN = 0x12,
	DYNAMIXEL_REGISTER_TORQUE_ENABLED = 0x18,
	DYNAMIXEL_REGISTER_LED = 0x19,
	DYNAMIXEL_REGISTER_CW_COMPLIANCE_MARGIN = 0x1a,
	DYNAMIXEL_REGISTER_CCW_COMPLIANCE_MARGIN = 0x1b,
	DYNAMIXEL_REGISTER_CW_COMPLIANCE_SLOPE = 0x1c,
	DYNAMIXEL_REGISTER_CCW_COMPLIANCE_SLOPE = 0x1d,
	DYNAMIXEL_REGISTER_GOAL_POSITION = 0x1e,
	DYNAMIXEL_REGISTER_MOVING_SPEED = 0x20,
	DYNAMIXEL_REGISTER_TORQUE_LIMIT = 0x22,
	DYNAMIXEL_REGISTER_PRESENT_POSITION = 0x24,
	DYNAMIXEL_REGISTER_PRESENT_SPEED    = 0x26,
	DYNAMIXEL_REGISTER_PRESENT_LOAD = 0x28,
	DYNAMIXEL_REGISTER_RESENT_VOLTAGE = 0x2a,
	DYNAMIXEL_REGISTER_PRESENT_TEMPERATURE = 0x2b,
	DYNAMIXEL_REGISTER_REGISTERED_INSTRUCTION = 0x2c,
	DYNAMIXEL_REGISTER_LOCK = 0x2f,
	DYNAMIXEL_REGISTER_PUNCH = 0x30,
};

typedef uint8_t dynamixelRegister_t;

typedef enum tag_dynamixel_port
{
	DYNAMIXEL_PORT_1 = 0, /* torso*/
	DYNAMIXEL_PORT_2 = 1, /* left leg */
	DYNAMIXEL_PORT_3 = 2,  /* right leg */
	DYNAMIXEL_PORT_CNT,

	DYNAMIXEL_PORT_ALL = 0xff
} dynamixel_port_t;

#define DYNAMIXEL_PORT_TORSO DYNAMIXEL_PORT_1
#define DYNAMIXEL_PORT_LEFT_LEG DYNAMIXEL_PORT_2
#define DYNAMIXEL_PORT_RIGHT_LEG DYNAMIXEL_PORT_3

#define DYNAMIXEL_MAX_RESPONSE_DELAY_MS 1U

#define DYNAMIXEL_BROADCAST_ID (0xfe)

typedef uint8_t dynamixel_motorID_t;

typedef uint8_t dynamixel_instruction_t;

typedef uint8_t dynamixel_register_t;

#define DYNAMIXEL_MAX_RESPONSE_PACKE_LEN 20


#endif /* DYNAMIXEL_CONFIG_H_ */

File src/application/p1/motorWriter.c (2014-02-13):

/*
 * motorWriter.c
 *
 *  Created on: Apr 10, 2013
 *      Author: lutz
 */


#include <flawless/init/systemInitializer.h>

#include <flawless/protocol/genericFlawLessProtocolApplication.h>
#include <flawless/timer/swTimer.h>

#include <flawless/core/msg_msgPump.h>
#include <flawless/config/msgIDs.h>

#include <flawless/rpc/RPC.h>

#include <interfaces/motorIDs.h>
#include <interfaces/offsets.h>
#include <interfaces/motorAssociations.h>

#include <interfaces/dynamixel_config.h>
#include <interfaces/dynamixel.h>

#include <interfaces/configuration.h>

#include <string.h>


MSG_PUMP_DECLARE_MESSAGE_BUFFER_POOL(motorButtonSwitchBP, uint8_t, 3, MSG_ID_USER_MOTOR_SWITCH)

#define SEND_COMPLIANCE_MARGIN_DELAY_MS 250U

#define COM_2_MAIN_COMPUTER_LOGIC_INTERFACE_NR 1U

/***********************************************************************************/
/***************************** motor initializazion values *************************/
/***********************************************************************************/

#define COMPLIANCE_MARGIN 1U
#define COMPLIANCE_SLOPE  16U
#define ALARM_SHUTDOWN 36U
#define TEMPERATURE_LIMIT 70U

#define DYNAMIXEL_RANGE_MAX 1023U

static const motorID_t allMotors[] = MOTORS_ALL;
static const motorID_t torsoMotors[] = MOTORS_TORSO;
static const motorID_t leftLegMotors[] = MOTORS_LEFT_LEG;
static const motorID_t rightLegMotors[] = MOTORS_RIGHT_LEG;

typedef struct tag_motorSetupValues
{
	uint8_t complianceMarginCW, complianceMarginCCW;
	uint8_t complianceSlopeCW, complianceSlopeCCW;
} motorSetupValue_t;

typedef motorSetupValue_t motorSetupValues_t[MOTOR_LAST_MOTOR];

static const motorSetupValues_t motorSetupDefaultValues =
{
		{0, 0, 3, 3}, /* head */
		{0, 0, 3, 3}, /* head */

		{2, 2, 16, 16}, /* arm */
		{2, 2, 16, 16}, /* arm */
		{2, 2, 16, 16}, /* arm */
		{2, 2, 16, 16}, /* arm */
		{2, 2, 16, 16}, /* arm */
		{2, 2, 16, 16}, /* arm */

		{1, 1, 16, 16}, /* leg */
		{1, 1, 16, 16}, /* leg */
		{1, 1, 16, 16}, /* leg */
		{1, 1, 16, 16}, /* leg */
		{1, 1, 16, 16}, /* leg */
		{1, 1, 16, 16}, /* leg */
		{1, 1, 16, 16}, /* leg */
		{1, 1, 16, 16}, /* leg */
		{1, 1, 16, 16}, /* leg */
		{1, 1, 16, 16}, /* leg */
		{1, 1, 16, 16}, /* leg */
		{1, 1, 16, 16}  /* leg */
};

CONFIG_VARIABLE(motorSetupValues_t, g_motorSetupValues, &motorSetupDefaultValues);


static void initializeMotors(void);


RPC_FUNCTION(setMotorSetupValues, "setMotorSetupValues", "setup the compliance margins and slopes for all motors", motorSetupValues_t, uint8_t, false, true)
	memcpy(g_motorSetupValues, i_param, sizeof(g_motorSetupValues));
	config_updateToFlash();
	initializeMotors();
	*((uint8_t*)o_param) = 1U;
}

typedef struct tag_motorPositionAnsSpeed_t {
	uint16_t position, speed;
} motorPositionAnsSpeed_t;

static void writeMotorValues(const void *i_packet, uint16_t i_packetLen, flawLessInterfaceDescriptor_t i_interfaceDescriptor);
GENERIC_PROTOCOL_ENDPOINT(writeMotorValues, 42)
static void writeMotorValues(const void *i_packet, uint16_t i_packetLen, flawLessInterfaceDescriptor_t i_interfaceDescriptor)
{
	if ((COM_2_MAIN_COMPUTER_LOGIC_INTERFACE_NR == i_interfaceDescriptor) &&
		(NULL != i_packet) &&
		(80 == i_packetLen))
	{
		const motorPositionAnsSpeed_t *values = (const motorPositionAnsSpeed_t*) i_packet;

		/* Write all torso motors */
		{
			uint8_t *dataPtrs[sizeof(torsoMotors)];
			motorID_t motorIDs[sizeof(torsoMotors)];
			uint8_t i;
			uint8_t motorCnt = 0;
			for (i = 0; i < sizeof(torsoMotors); ++i)
			{
				if ((values[torsoMotors[i] - 1U].position <= DYNAMIXEL_RANGE_MAX) && values[torsoMotors[i] - 1U].speed <= DYNAMIXEL_RANGE_MAX)
				{
					dataPtrs[motorCnt] = (uint8_t*)&(values[torsoMotors[i] - 1U]);
					motorIDs[motorCnt] = torsoMotors[i];
					++motorCnt;
				}
			}
			addOffsets(motorIDs, motorCnt, (uint16_t**)dataPtrs);
			dynamixel_sync_write(motorIDs, motorCnt, DYNAMIXEL_REGISTER_GOAL_POSITION, (const uint8_t**)dataPtrs, 4, DYNAMIXEL_PORT_TORSO, DYNAMIXEL_TRANSACTION_PRIORITY_HIGH);
		}

		/* Write all left leg motors */
		{
			uint8_t *dataPtrs[sizeof(leftLegMotors)];
			motorID_t motorIDs[sizeof(leftLegMotors)];
			uint8_t i;
			uint8_t motorCnt = 0;
			for (i = 0; i < sizeof(leftLegMotors); ++i)
			{
				if ((values[leftLegMotors[i] - 1U].position <= DYNAMIXEL_RANGE_MAX) && values[leftLegMotors[i] - 1U].speed <= DYNAMIXEL_RANGE_MAX)
				{
					dataPtrs[motorCnt] = (uint8_t*)&(values[leftLegMotors[i] - 1U]);
					motorIDs[motorCnt] = leftLegMotors[i];
					++motorCnt;
				}
			}
			addOffsets(motorIDs, motorCnt, (uint16_t**)dataPtrs);
			dynamixel_sync_write(motorIDs, motorCnt, DYNAMIXEL_REGISTER_GOAL_POSITION, (const uint8_t**)dataPtrs, 4, DYNAMIXEL_PORT_LEFT_LEG, DYNAMIXEL_TRANSACTION_PRIORITY_HIGH);
		}

		/* Write all right leg motors */
		{
			uint8_t *dataPtrs[sizeof(rightLegMotors)];
			motorID_t motorIDs[sizeof(rightLegMotors)];
			uint8_t i;
			uint8_t motorCnt = 0;
			for (i = 0; i < sizeof(rightLegMotors); ++i)
			{
				if ((values[rightLegMotors[i] - 1U].position <= DYNAMIXEL_RANGE_MAX) && values[rightLegMotors[i] - 1U].speed <= DYNAMIXEL_RANGE_MAX)
				{
					dataPtrs[motorCnt] = (uint8_t*)&(values[rightLegMotors[i] - 1U]);
					motorIDs[motorCnt] = rightLegMotors[i];
					++motorCnt;
				}
			}
			addOffsets(motorIDs, motorCnt, (uint16_t**)dataPtrs);
			dynamixel_sync_write(motorIDs, motorCnt, DYNAMIXEL_REGISTER_GOAL_POSITION, (const uint8_t**)dataPtrs, 4, DYNAMIXEL_PORT_RIGHT_LEG, DYNAMIXEL_TRANSACTION_PRIORITY_HIGH);
		}
	}
}


static void setupMotors(void);
static void setupMotors(void)
{
	/* send a "shut up" message to every motor */
	uint8_t returnDelayTime = 40U;
	uint8_t statusReturnLevel = 1U;
	uint16_t movingSpeed = 0U;

	for (dynamixel_port_t port = DYNAMIXEL_PORT_1; port < DYNAMIXEL_PORT_CNT; ++port)
	{
		dynamixel_write(DYNAMIXEL_BROADCAST_ID, DYNAMIXEL_REGISTER_STATUS_RETURN_LEVEL, (uint8_t*)&statusReturnLevel, sizeof(statusReturnLevel), port, NULL, false, DYNAMIXEL_TRANSACTION_PRIORITY_HIGH);
		dynamixel_write(DYNAMIXEL_BROADCAST_ID, DYNAMIXEL_REGISTER_RETURN_DELAY_TIME, (uint8_t*)&returnDelayTime, sizeof(returnDelayTime), port, NULL, false, DYNAMIXEL_TRANSACTION_PRIORITY_HIGH);
		dynamixel_write(DYNAMIXEL_BROADCAST_ID, DYNAMIXEL_REGISTER_MOVING_SPEED, (uint8_t*)&movingSpeed, sizeof(movingSpeed), port, NULL, false, DYNAMIXEL_TRANSACTION_PRIORITY_HIGH);
	}
}
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

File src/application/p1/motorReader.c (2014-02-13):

/*
 * motors.c
 *
 *  Created on: Mar 7, 2013
 *      Author: lutz
 */

#include <flawless/init/systemInitializer.h>
#include <flawless/timer/swTimer.h>
#include <flawless/core/msg_msgPump.h>
#include <flawless/config/msgIDs.h>
#include <flawless/protocol/genericFlawLessProtocolApplication.h>
#include <flawless/protocol/genericFlawLessProtocol_Data.h>
#include <flawless/rpc/RPC.h>

#include <interfaces/dynamixel.h>
#include <interfaces/dynamixel_config.h>
#include <interfaces/motorIDs.h>
#include <interfaces/motorAssociations.h>

#include <interfaces/systemTime.h>
#include <interfaces/offsets.h>

#include <string.h>

#define COM_2_MAIN_COMPUTER_LOGIC_INTERFACE_NR 1U

MSG_PUMP_DECLARE_MESSAGE_BUFFER_POOL(triggerPushMotorValuesBP, int, 2, MSG_ID_TRIGGER_PUSH_MOTOR_VALUES)
MSG_PUMP_DECLARE_MESSAGE_BUFFER_POOL(triggerReadMotorValuesBP, int, 2, MSG_ID_TRIGGER_READ_MOTORS)

static const motorID_t torsoMotors[] = MOTORS_TORSO;
static const motorID_t leftLegMotors[] = MOTORS_LEFT_LEG;
static const motorID_t rightLegMotors[] = MOTORS_RIGHT_LEG;

#define MOTOR_READ_CYCLE_INTERVAL_MS 4U

#define MOTOR_DISTRIBUTE_INTERVAL_MS 10U


typedef struct tag_motorPosition
{
	int16_t position;
	int16_t speed;
	int16_t load;
} motorPosition_t;

typedef struct tag_motorInfo
{
	uint16_t successfullReads, missedReads;
	uint8_t error;
	uint8_t consecutiveFailedReads;
} motorInfo_t;

typedef int16_t motorPositionsArray_t[MOTOR_LAST_MOTOR];

static motorPosition_t g_motorPositions[MOTOR_LAST_MOTOR] = {{0, 0, 0}};
static motorPositionsArray_t g_motorPositionsNotAdjustedOffsets = {0};
static motorInfo_t g_motorInfos[MOTOR_LAST_MOTOR] = {{0, 0, 0, 0}};

static uint32_t g_totalSuccessfullReads = 0U;
static uint32_t g_totalUnsuccessfullReads = 0U;

#define MAX_CONSECUTIVE_READ_FAILURES 5U

static void onMotorRead(bool success,
						const uint8_t *receivedData,
						uint8_t receivedDataCnt,
						uint8_t error,
						dynamixel_motorID_t motor,
						dynamixel_instruction_t instruction)
{
	if (FALSE == success)
	{
		if ((motor <= MOTOR_LAST_MOTOR))
		{
			++g_totalUnsuccessfullReads;
			++(g_motorInfos[motor - MOTOR_FIRST_MOTOR].missedReads);
			if (g_motorInfos[motor - MOTOR_FIRST_MOTOR].consecutiveFailedReads >= (MAX_CONSECUTIVE_READ_FAILURES - 1U))
			{
				g_motorPositions[motor - MOTOR_FIRST_MOTOR].position = -1;
				g_motorPositionsNotAdjustedOffsets[motor - MOTOR_FIRST_MOTOR] = -1;
			} else
			{
				++(g_motorInfos[motor - MOTOR_FIRST_MOTOR].consecutiveFailedReads);
			}
		}
	} else
	{
		if ((motor <= MOTOR_LAST_MOTOR) &&
			(DYNAMIXEL_INSTRUCTION_READ == instruction) &&
			(sizeof(motorPosition_t) == receivedDataCnt))
		{
			const motorPosition_t *motorValues = (const motorPosition_t*)receivedData;
			++g_totalSuccessfullReads;
			++(g_motorInfos[motor - MOTOR_FIRST_MOTOR].successfullReads);
			g_motorInfos[motor - MOTOR_FIRST_MOTOR].error = error;
			g_motorInfos[motor - MOTOR_FIRST_MOTOR].consecutiveFailedReads = 0;

			g_motorPositions[motor - MOTOR_FIRST_MOTOR].position = motorValues->position;
			g_motorPositionsNotAdjustedOffsets[motor - MOTOR_FIRST_MOTOR] = motorValues->position;

			uint16_t *positionPtr = (uint16_t*)&(g_motorPositions[motor - MOTOR_FIRST_MOTOR].position);

			removeOffsets(&motor, sizeof(motor), &positionPtr);
			if (0 != (motorValues->speed & 0x0400)) /* this means a negative number */
			{
				g_motorPositions[motor - MOTOR_FIRST_MOTOR].speed = - (motorValues->speed & 0x03ff);
			} else {
				g_motorPositions[motor - MOTOR_FIRST_MOTOR].speed =   (motorValues->speed & 0x03ff);
			}

			if (0 != (motorValues->load & 0x0400)) /* this means a negative number */
			{
				g_motorPositions[motor - MOTOR_FIRST_MOTOR].load = - (motorValues->load & 0x03ff);
			} else {
				g_motorPositions[motor - MOTOR_FIRST_MOTOR].load =   (motorValues->load & 0x03ff);
			}
		}
	}
}

RPC_FUNCTION(getRawMotorPositions, "getRawMotorPositions", "retreive the motorvalues without offsets", uint8_t, motorPositionsArray_t, true, false)
	memcpy(o_param, g_motorPositionsNotAdjustedOffsets, sizeof(g_motorPositionsNotAdjustedOffsets));
}

static void onTriggerPushUp(void);
static void onTriggerPushUp(void)
{
	int *blubb = NULL;
	msgPump_getFreeBuffer(MSG_ID_TRIGGER_PUSH_MOTOR_VALUES, (void*)&blubb);
	if (NULL != blubb)
	{
		msgPump_postMessage(MSG_ID_TRIGGER_PUSH_MOTOR_VALUES, blubb);
	}
}

static void onPushDataToOdroid(const msgPump_MsgID_t msgID, const void *data)
{
	if ((MSG_ID_TRIGGER_PUSH_MOTOR_VALUES == msgID) &&
		(NULL != data))
	{
		static systemTime_t startTime = 0;
		if (0 == startTime)
		{
			startTime = getSystemTimeUS();
		}
		systemTime_t timeElapsed = getSystemTimeUS() - startTime;

		genericProtocol_sendMessage(1, 42, sizeof(g_motorPositions), &g_motorPositions);

		if (timeElapsed >= 2000000ULL)
		{
			uint8_t i = 0U;
			genericProtocol_sendMessage(1, 43, sizeof(g_motorInfos), &g_motorInfos);
			/* reset statistics */
			for (i = 0U; i <= MOTOR_LAST_MOTOR - MOTOR_FIRST_MOTOR; ++i)
			{
				g_motorInfos[i].missedReads     = 0U;
				g_motorInfos[i].successfullReads = 0U;
			}

			startTime = getSystemTimeUS();
			g_totalSuccessfullReads = 0U;
			g_totalUnsuccessfullReads = 0U;
		}
	}
}

static void onReadMotors(const msgPump_MsgID_t msgID, const void *data)
{
	if ((MSG_ID_TRIGGER_READ_MOTORS == msgID) &&
		(NULL != data))
	{

		bool readSuccess = true;


		for (uint8_t i = 0U; i < (sizeof(torsoMotors) / sizeof(torsoMotors[0])); ++i)
		{
			readSuccess &= dynamixel_read(torsoMotors[i], DYNAMIXEL_REGISTER_PRESENT_POSITION, 6, DYNAMIXEL_PORT_TORSO, &onMotorRead, DYNAMIXEL_TRANSACTION_PRIORITY_LOW);
		}

		for (uint8_t i = 0U; i < (sizeof(leftLegMotors) / sizeof(leftLegMotors[0])); ++i)
		{
			readSuccess &= dynamixel_read(leftLegMotors[i], DYNAMIXEL_REGISTER_PRESENT_POSITION, 6, DYNAMIXEL_PORT_LEFT_LEG, &onMotorRead, DYNAMIXEL_TRANSACTION_PRIORITY_LOW);
		}

		for (uint8_t i = 0U; i < (sizeof(rightLegMotors) / sizeof(rightLegMotors[0])); ++i)
		{
			readSuccess &= dynamixel_read(rightLegMotors[i], DYNAMIXEL_REGISTER_PRESENT_POSITION, 6, DYNAMIXEL_PORT_RIGHT_LEG, &onMotorRead, DYNAMIXEL_TRANSACTION_PRIORITY_LOW);
		}
	}
}

static void triggerReadMotors(void);
static void triggerReadMotors(void)
{
	int *blubb = NULL;
	msgPump_getFreeBuffer(MSG_ID_TRIGGER_READ_MOTORS, (void*)&blubb);
	if (NULL != blubb)
	{
		msgPump_postMessage(MSG_ID_TRIGGER_READ_MOTORS, blubb);
	}
}

#include "interfaces/systemTime.h"

#include <libopencm3/stm32/f4/dma.h>
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

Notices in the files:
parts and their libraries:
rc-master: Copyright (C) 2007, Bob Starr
